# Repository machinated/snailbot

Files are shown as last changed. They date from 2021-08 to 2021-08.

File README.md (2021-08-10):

# snailbot
Arduino compatible robot platform

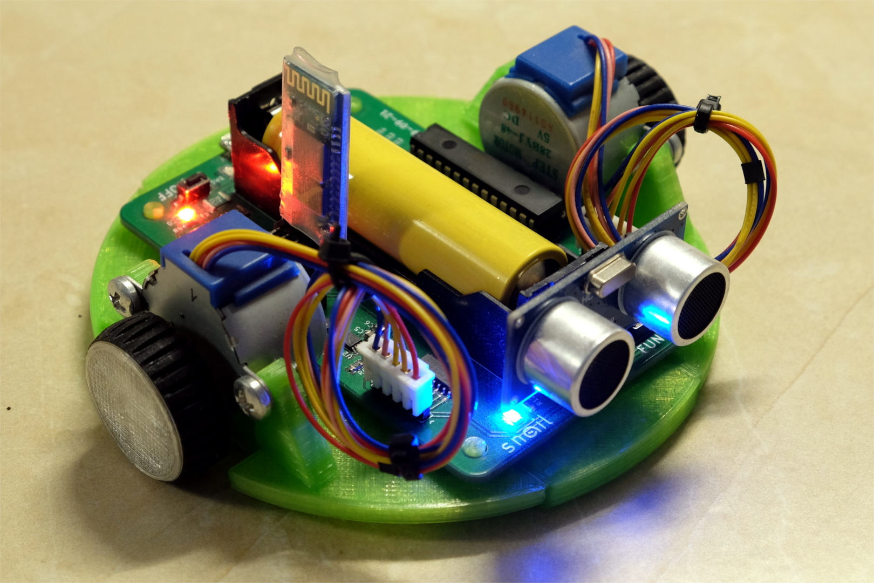
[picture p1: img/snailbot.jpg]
snailbot picture


## Hardware
List of parts:
 - electronic components listed in the [BOM file](pcb/BOM.csv)
 - HC-SR04 ultrasonic distance sensor
 - HC05 bluetooth adapter
 - 18650 lithium-ion battery
 - 2x 28BYJ-48 stepper motors

## Dependencies
- AccelStepper v.1.59

## Chassis
For better traction, use TPU for the tires.

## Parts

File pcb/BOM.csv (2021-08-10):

Item | Qty | Reference(s) | Value | Footprint
1 | 1 | BT1 | Battery_Cell | mc_mech:BatteryHolder_1x18650
2 | 1 | C1 | 4u7 | Capacitor_SMD:C_0805_2012Metric_Pad1.15x1.40mm_HandSolder
3 | 5 | C2, C4, C5, C6, C7 | 10u | Capacitor_SMD:C_0805_2012Metric_Pad1.15x1.40mm_HandSolder
4 | 4 | C8, C9, C10, C13 | 100n | Capacitor_SMD:C_0805_2012Metric_Pad1.15x1.40mm_HandSolder
5 | 2 | C11, C12 | 22p | Capacitor_SMD:C_0805_2012Metric_Pad1.15x1.40mm_HandSolder
6 | 1 | D1 | RED | LED_SMD:LED_1206_3216Metric_Pad1.42x1.75mm_HandSolder
7 | 1 | D2 | D_TVS | Diode_SMD:D_SMB_Handsoldering
8 | 1 | D3 | YELLOW | LED_SMD:LED_1206_3216Metric_Pad1.42x1.75mm_HandSolder
9 | 2 | D4, D5 | BLUE | LED_SMD:LED_1206_3216Metric_Pad1.42x1.75mm_HandSolder
10 | 1 | F1 | 750mA | Fuse:Fuse_1812_4532Metric_Pad1.30x3.40mm_HandSolder
11 | 1 | F2 | 1A | Fuse:Fuse_1812_4532Metric_Pad1.30x3.40mm_HandSolder
12 | 1 | J1 | USB_B_Micro | mc_mech:USB_Micro-B_MOLEX_105017-0001
13 | 1 | J2 | Conn_01x04_Female | Connector_PinHeader_2.54mm:PinHeader_1x04_P2.54mm_Vertical
14 | 2 | J3, J5 | Conn_01x05_Male | Connector_PinHeader_2.54mm:PinHeader_1x05_P2.54mm_Vertical
15 | 1 | J4 | Conn_01x06_Female | Connector_PinHeader_2.54mm:PinHeader_1x06_P2.54mm_Vertical
16 | 1 | L1 | 4u7 | Inductor_SMD:L_1210_3225Metric_Pad1.42x2.65mm_HandSolder
17 | 3 | R4, R9, R12 | 470 | Resistor_SMD:R_0805_2012Metric_Pad1.15x1.40mm_HandSolder
18 | 1 | R2 | 2k2 | Resistor_SMD:R_0805_2012Metric_Pad1.15x1.40mm_HandSolder
19 | 1 | R3 | 470k 1% | Resistor_SMD:R_0805_2012Metric_Pad1.15x1.40mm_HandSolder
20 | 1 | R5 | 1M | Resistor_SMD:R_0805_2012Metric_Pad1.15x1.40mm_HandSolder
21 | 1 | R6 | 150k 1% | Resistor_SMD:R_0805_2012Metric_Pad1.15x1.40mm_HandSolder
22 | 2 | R1, R7 | 1k | Resistor_SMD:R_0805_2012Metric_Pad1.15x1.40mm_HandSolder
23 | 1 | R8 | 100k | Resistor_SMD:R_0805_2012Metric_Pad1.15x1.40mm_HandSolder
24 | 3 | R10, R13, R15 | 10k | Resistor_SMD:R_0805_2012Metric_Pad1.15x1.40mm_HandSolder
25 | 1 | R11 | 15k | Resistor_SMD:R_0805_2012Metric_Pad1.15x1.40mm_HandSolder
26 | 2 | R14, R16 | 100 | Resistor_SMD:R_0805_2012Metric_Pad1.15x1.40mm_HandSolder
27 | 3 | SW1, SW2, SW3 | SW_Push | Button_Switch_SMD:SW_SPST_CK_RS282G05A3
28 | 1 | U1 | MCP73831-2-OT | Package_TO_SOT_SMD:SOT-23-5
29 | 1 | U2 | MCP1642B | Package_SO:MSOP-8-1EP_3x3mm_P0.65mm_EP2.54x2.8mm
30 | 2 | U3, U5 | ULN2003 | Package_SO:SOIC-16_3.9x9.9mm_P1.27mm
31 | 1 | U4 | ATmega328P-PU | Package_DIP:DIP-28_W7.62mm
32 | 1 | Y1 | 16MHz | Crystal:Crystal_HC49-U_Vertical

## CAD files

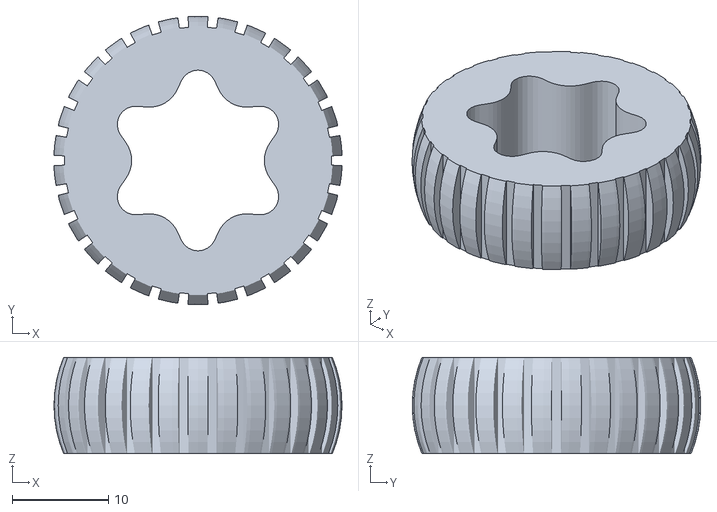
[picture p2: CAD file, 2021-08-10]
3d/stl/tire.stl
30.0 x 30.0 x 10.0

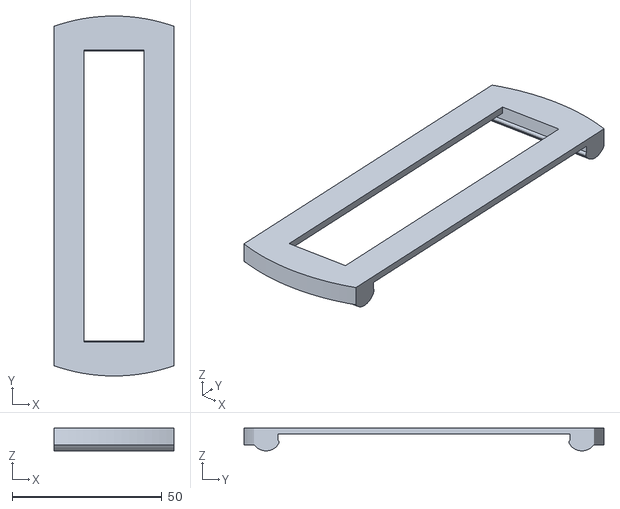
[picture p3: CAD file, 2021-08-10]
3d/stl/chassis_p2.stl
39.9 x 120.0 x 7.60

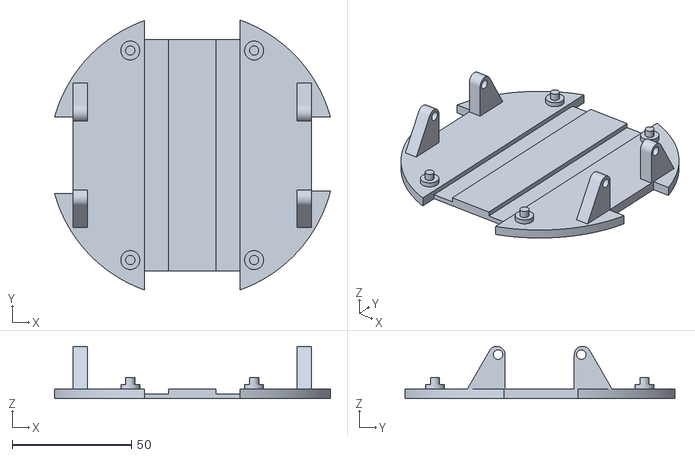
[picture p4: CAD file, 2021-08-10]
3d/stl/chassis_p1.stl
115.9 x 113.4 x 22.0

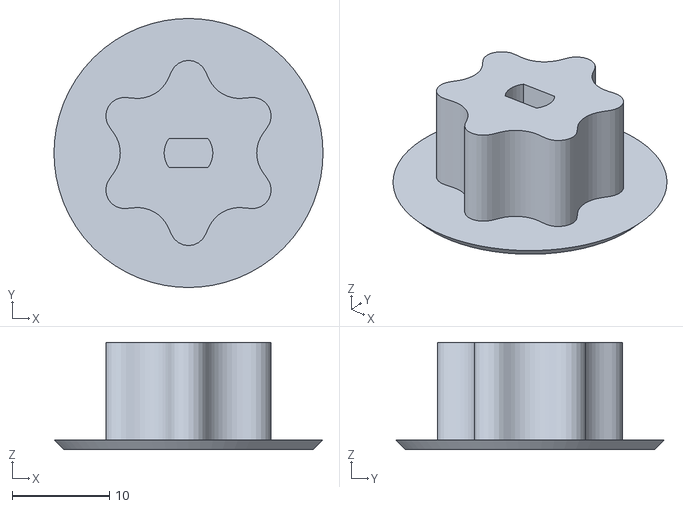
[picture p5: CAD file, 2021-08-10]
3d/stl/wheel.stl
27.6 x 27.6 x 11.0

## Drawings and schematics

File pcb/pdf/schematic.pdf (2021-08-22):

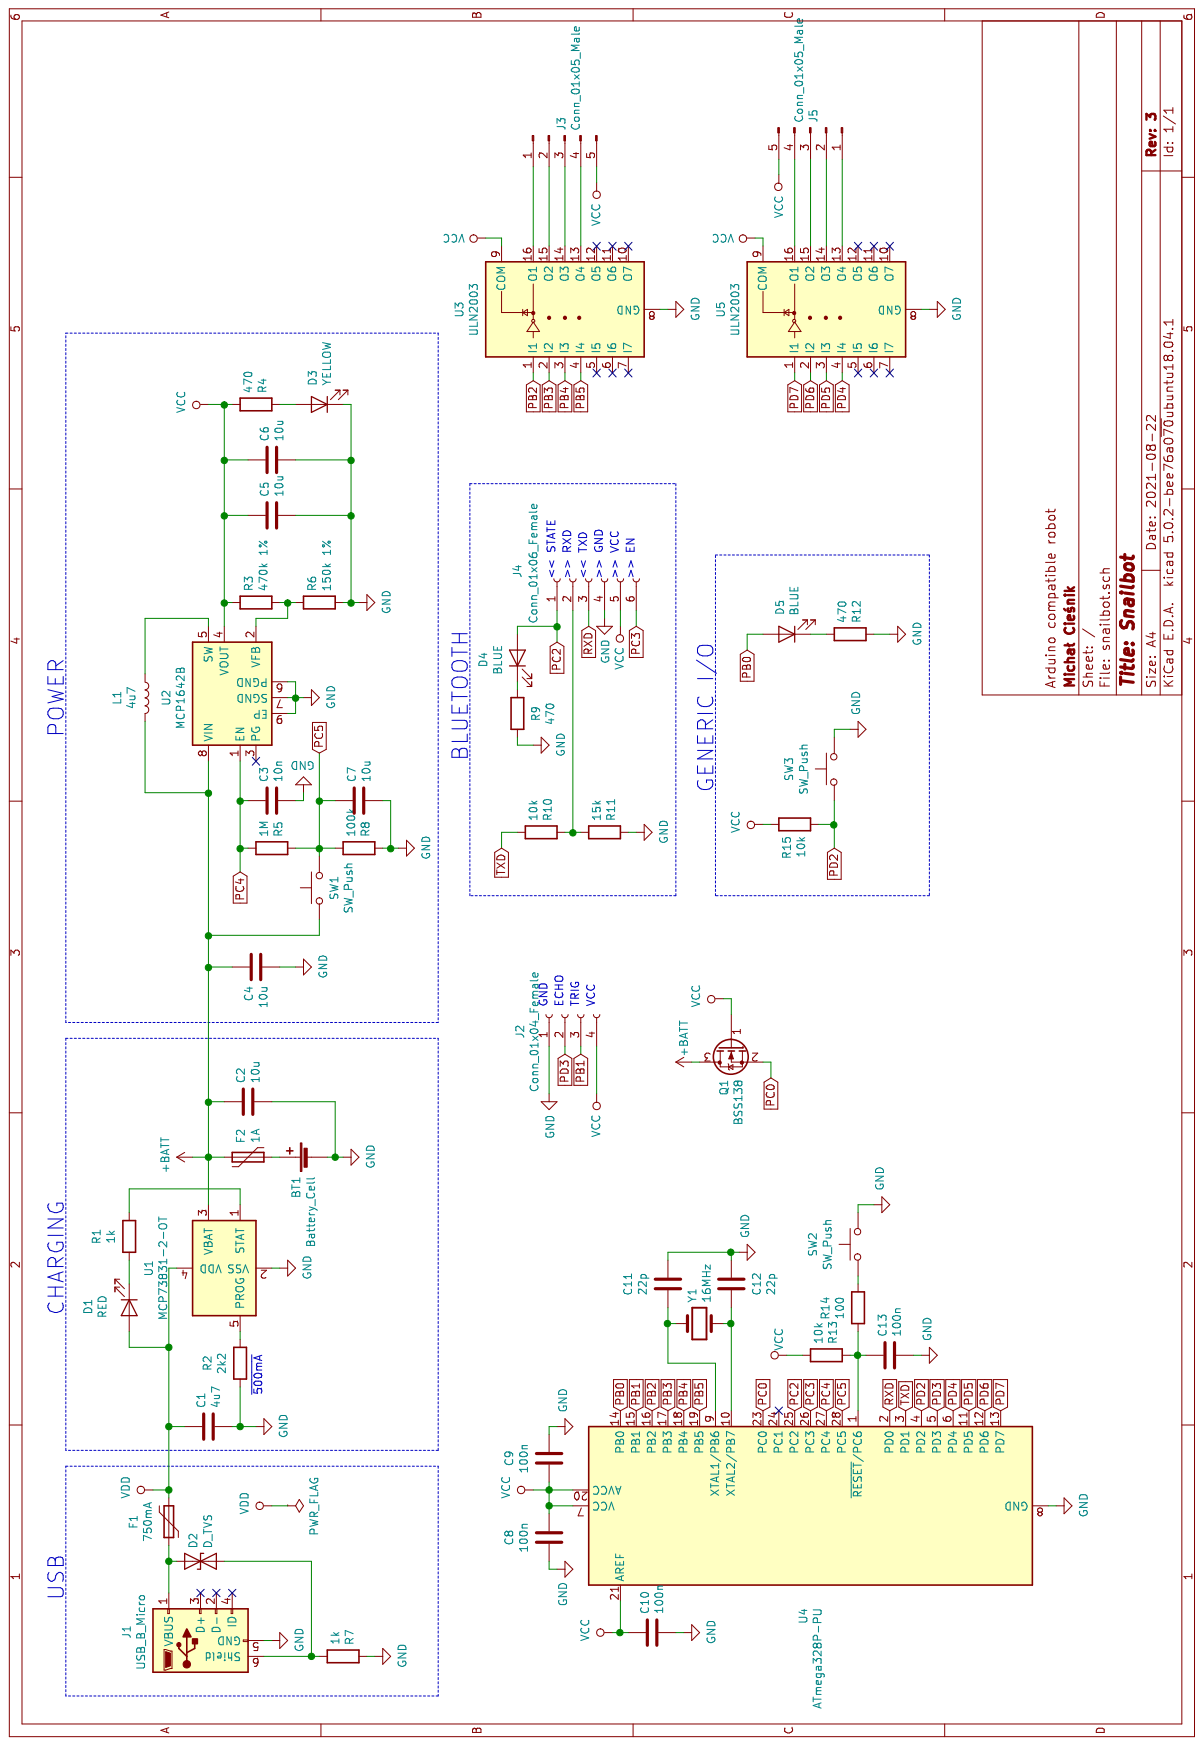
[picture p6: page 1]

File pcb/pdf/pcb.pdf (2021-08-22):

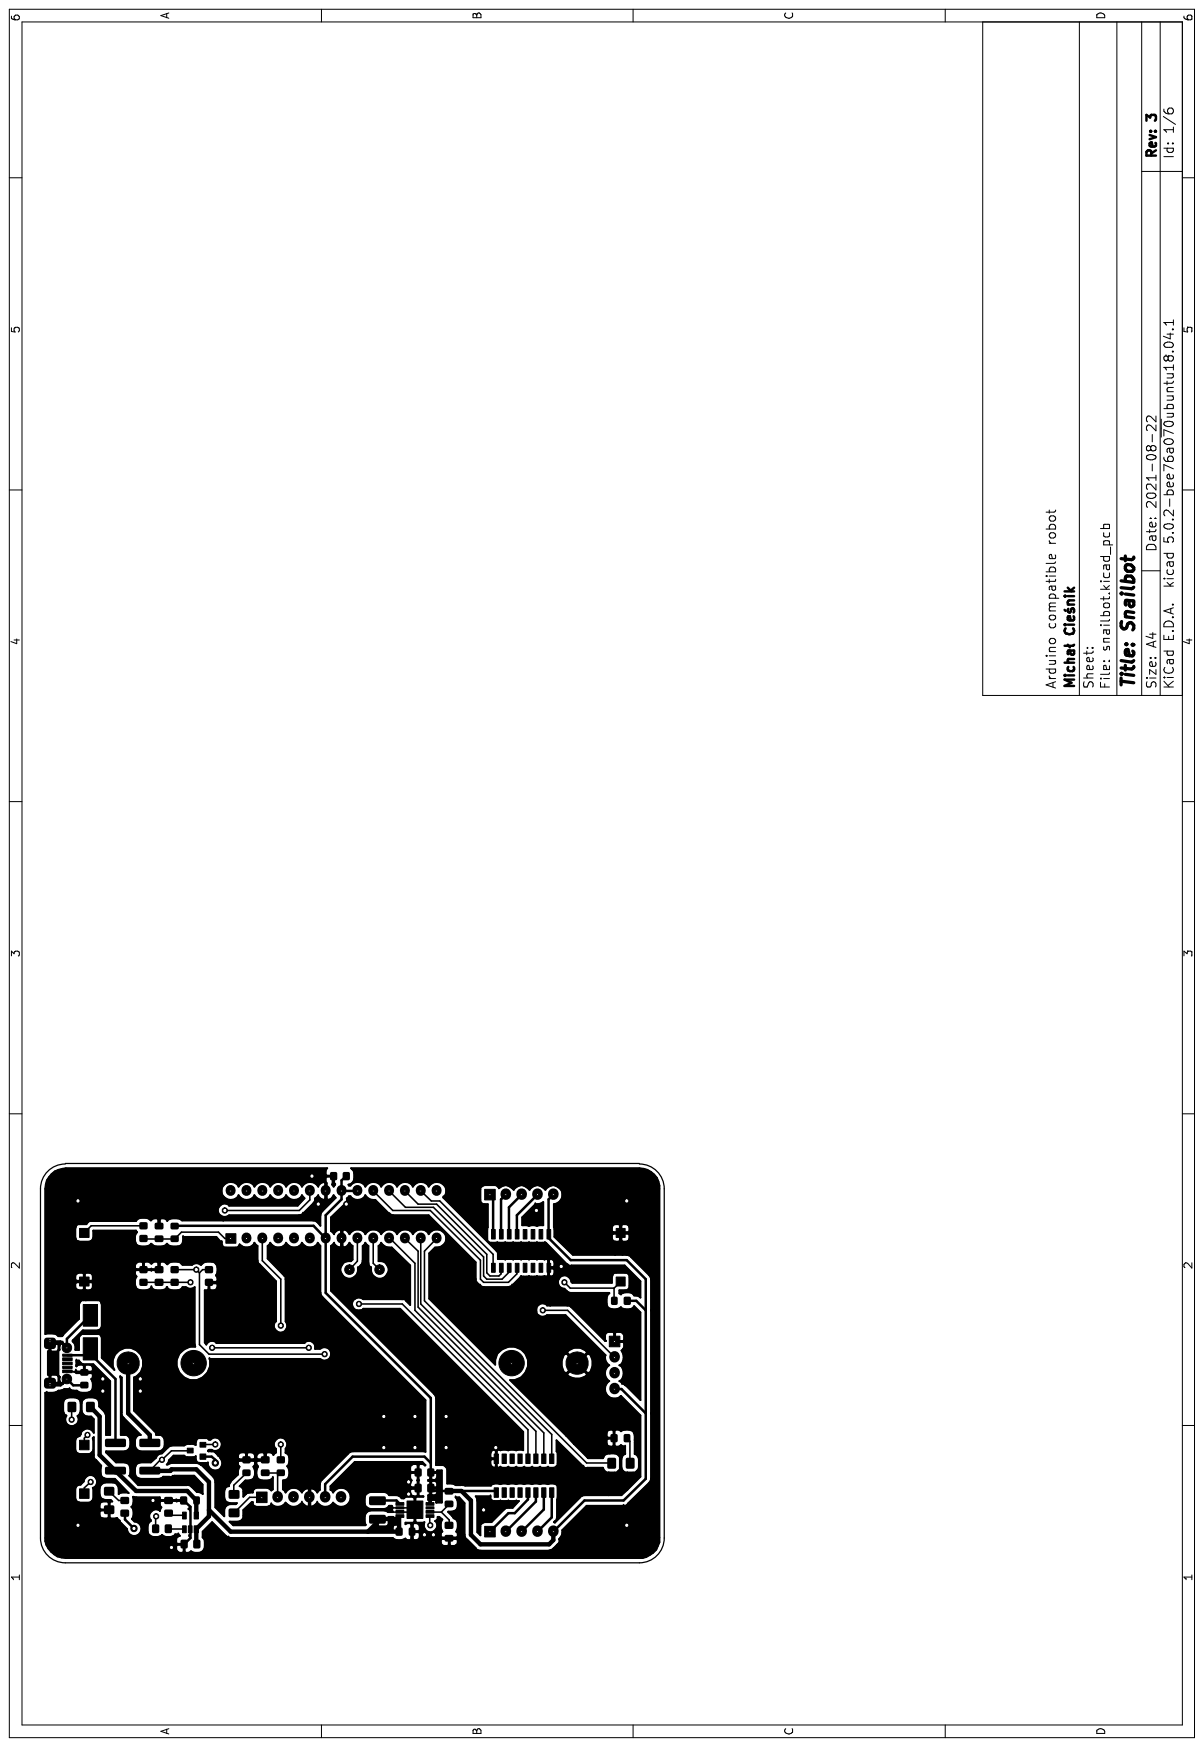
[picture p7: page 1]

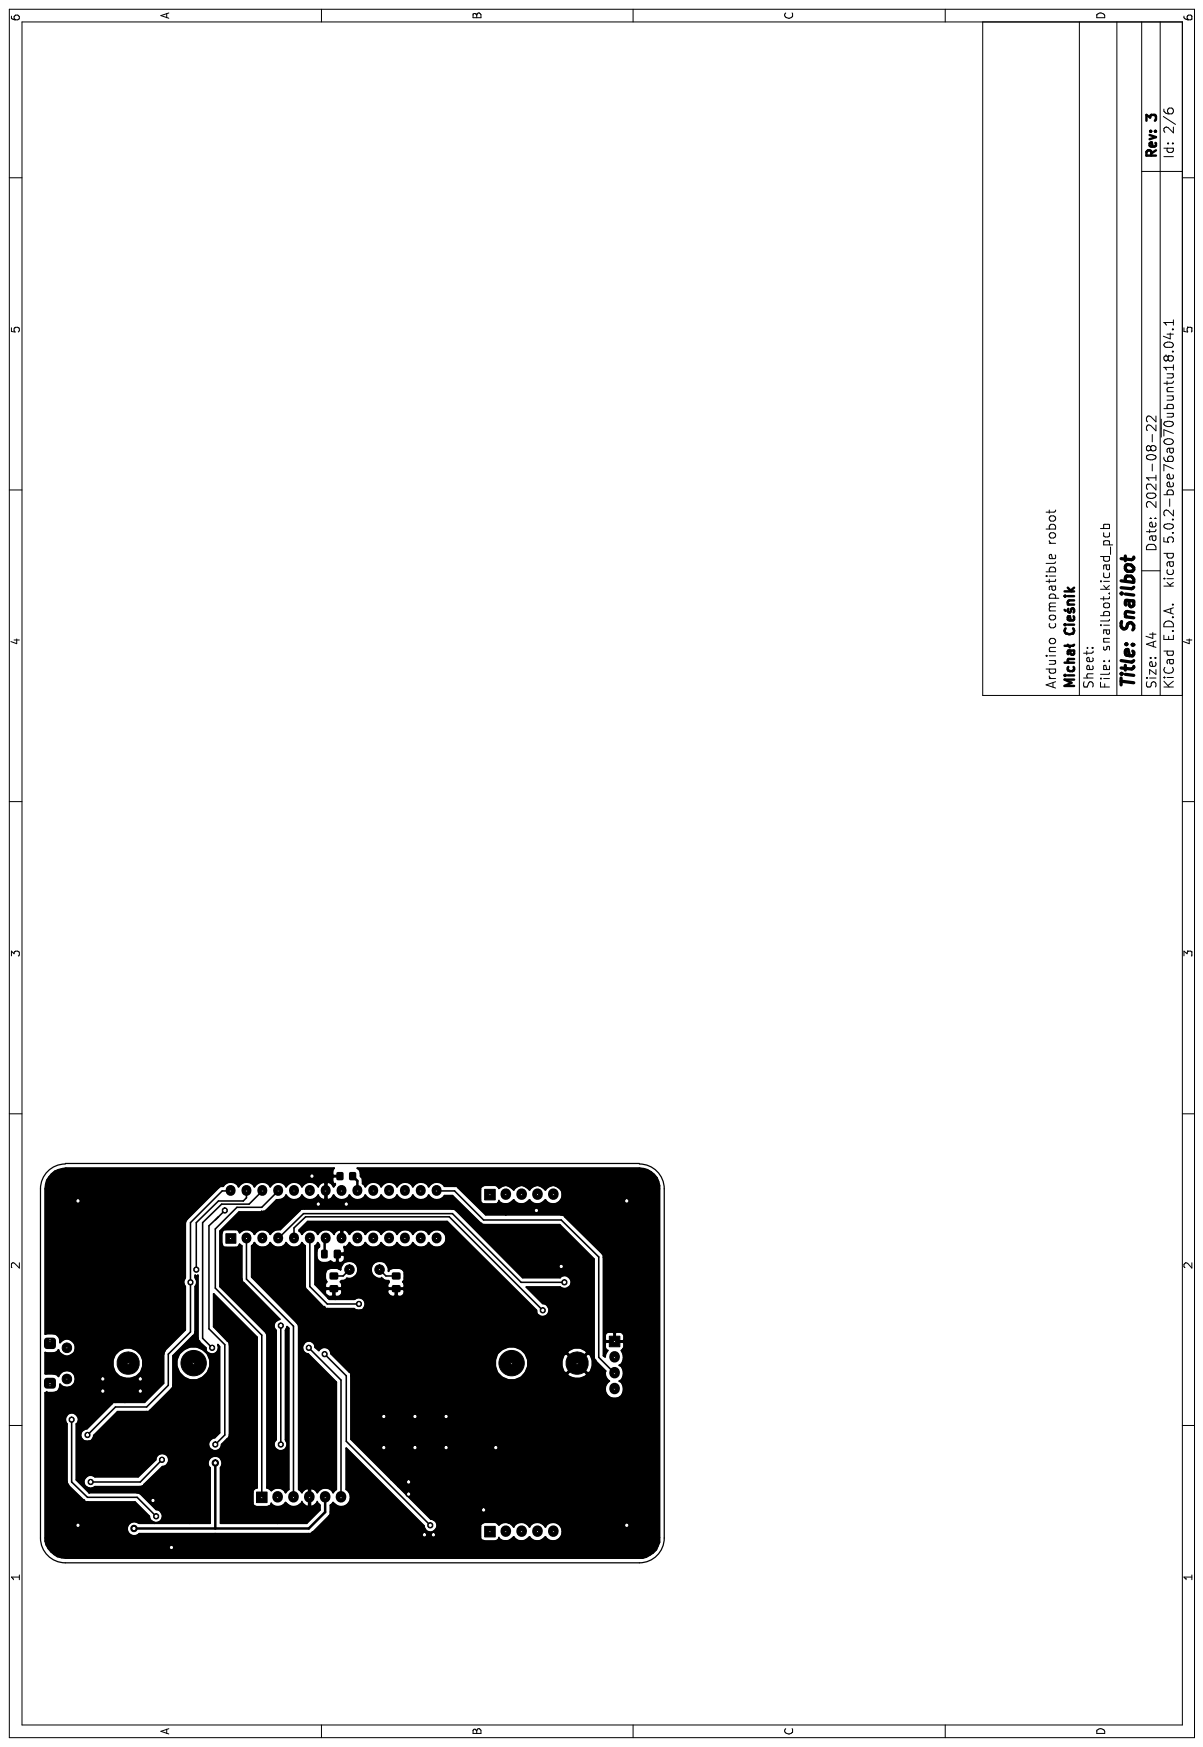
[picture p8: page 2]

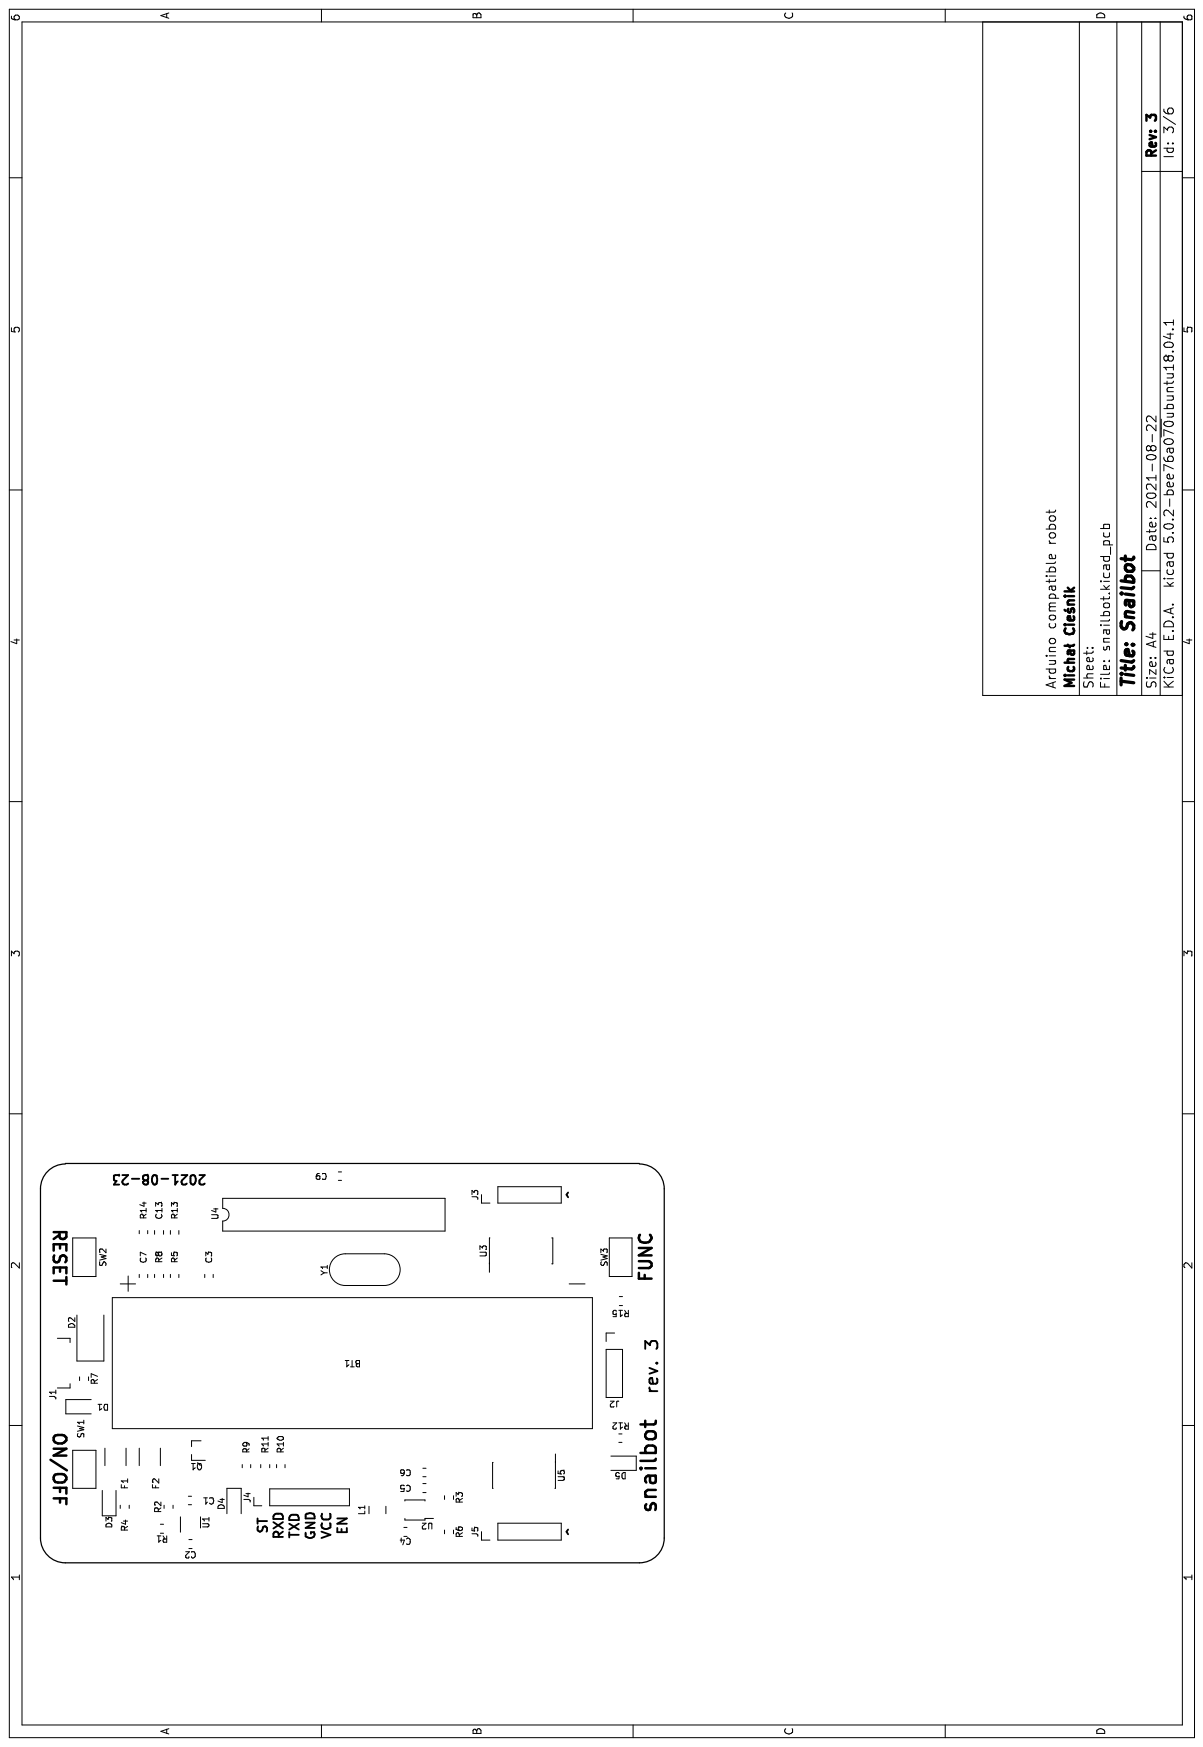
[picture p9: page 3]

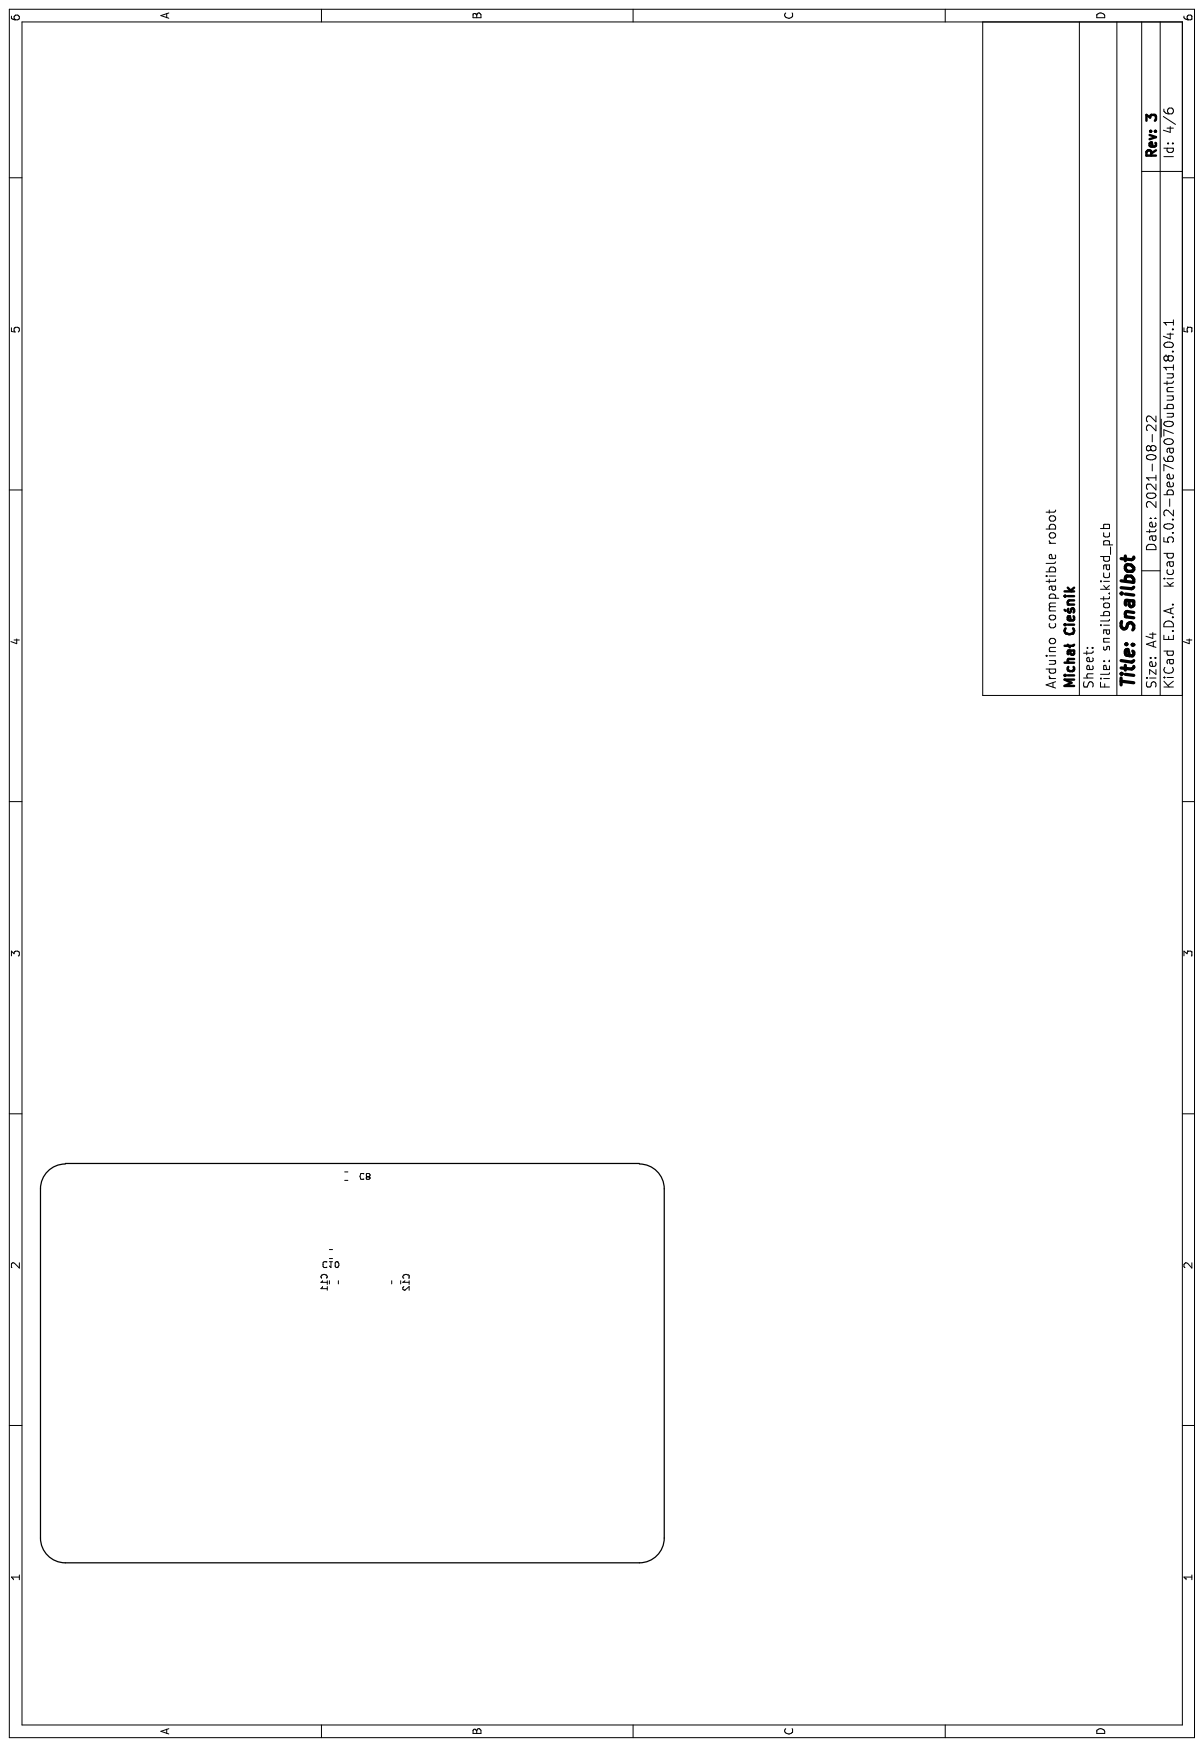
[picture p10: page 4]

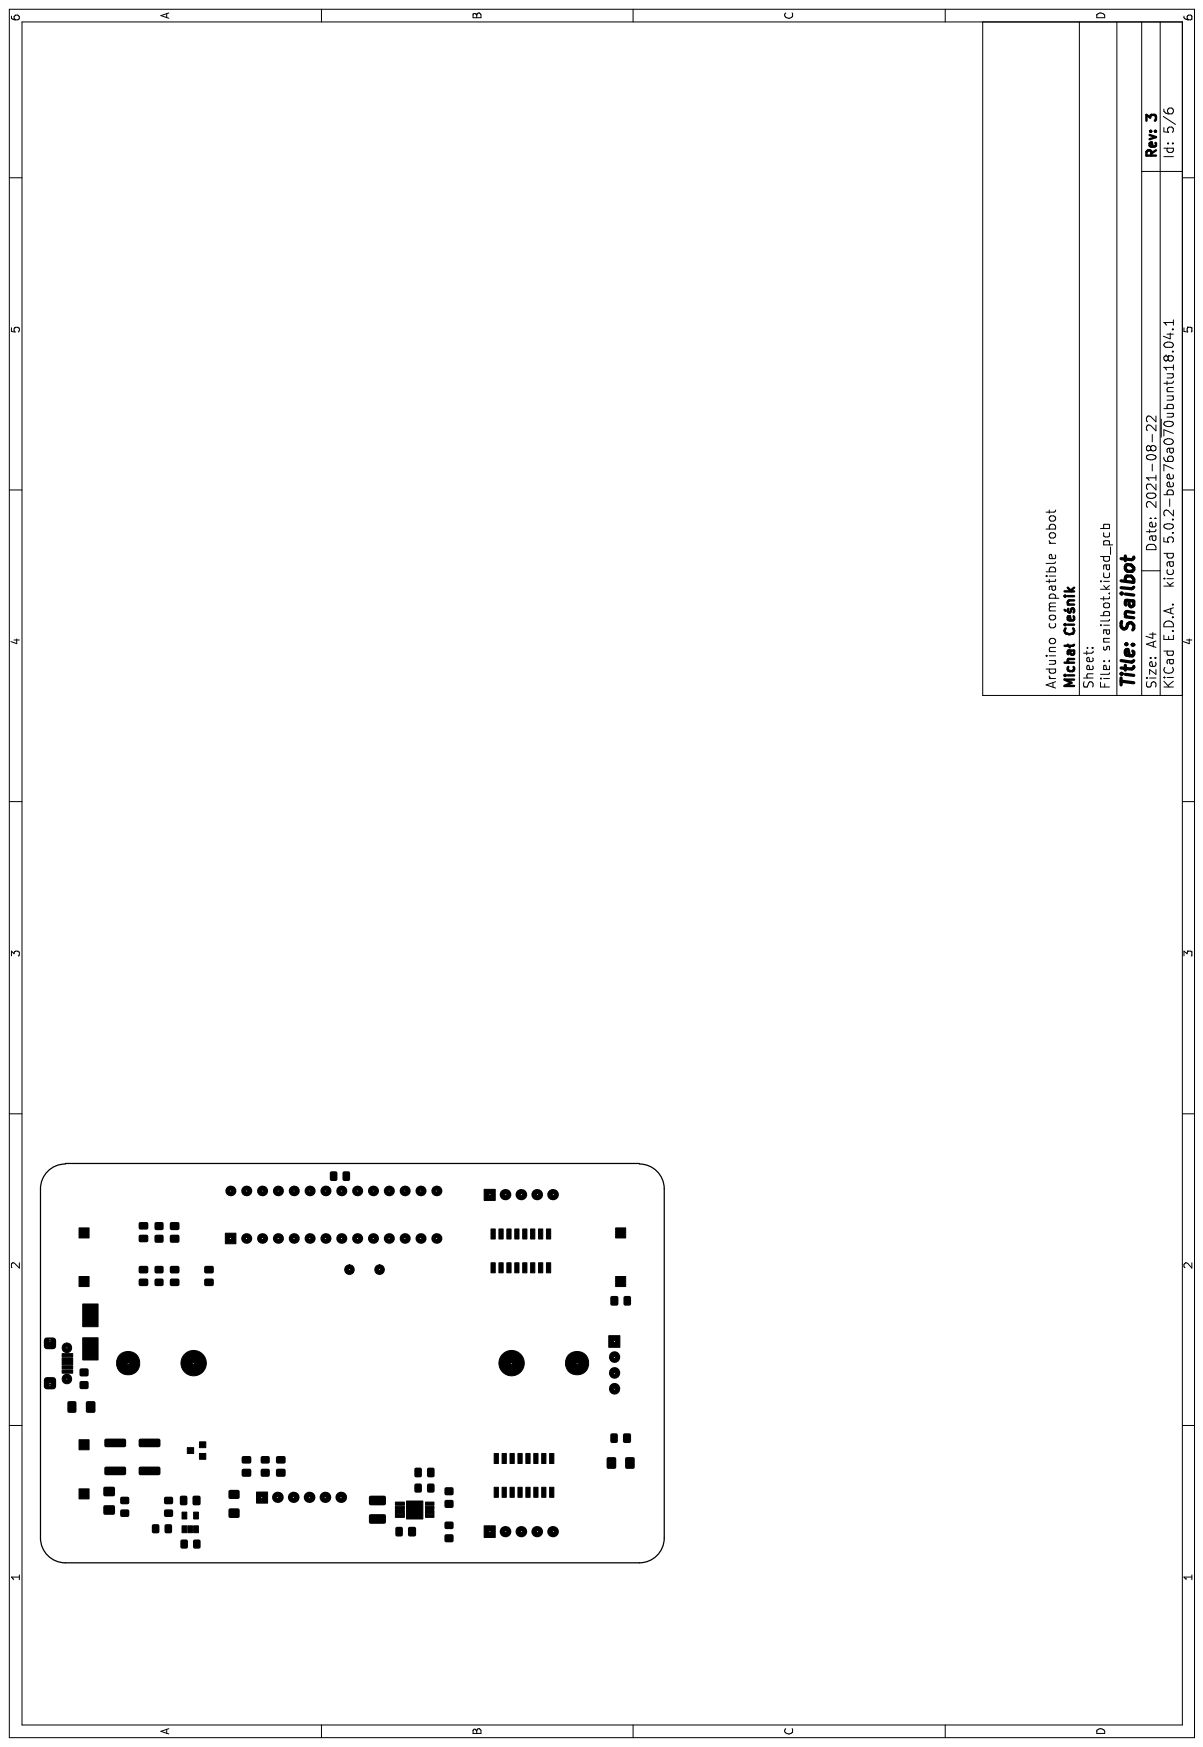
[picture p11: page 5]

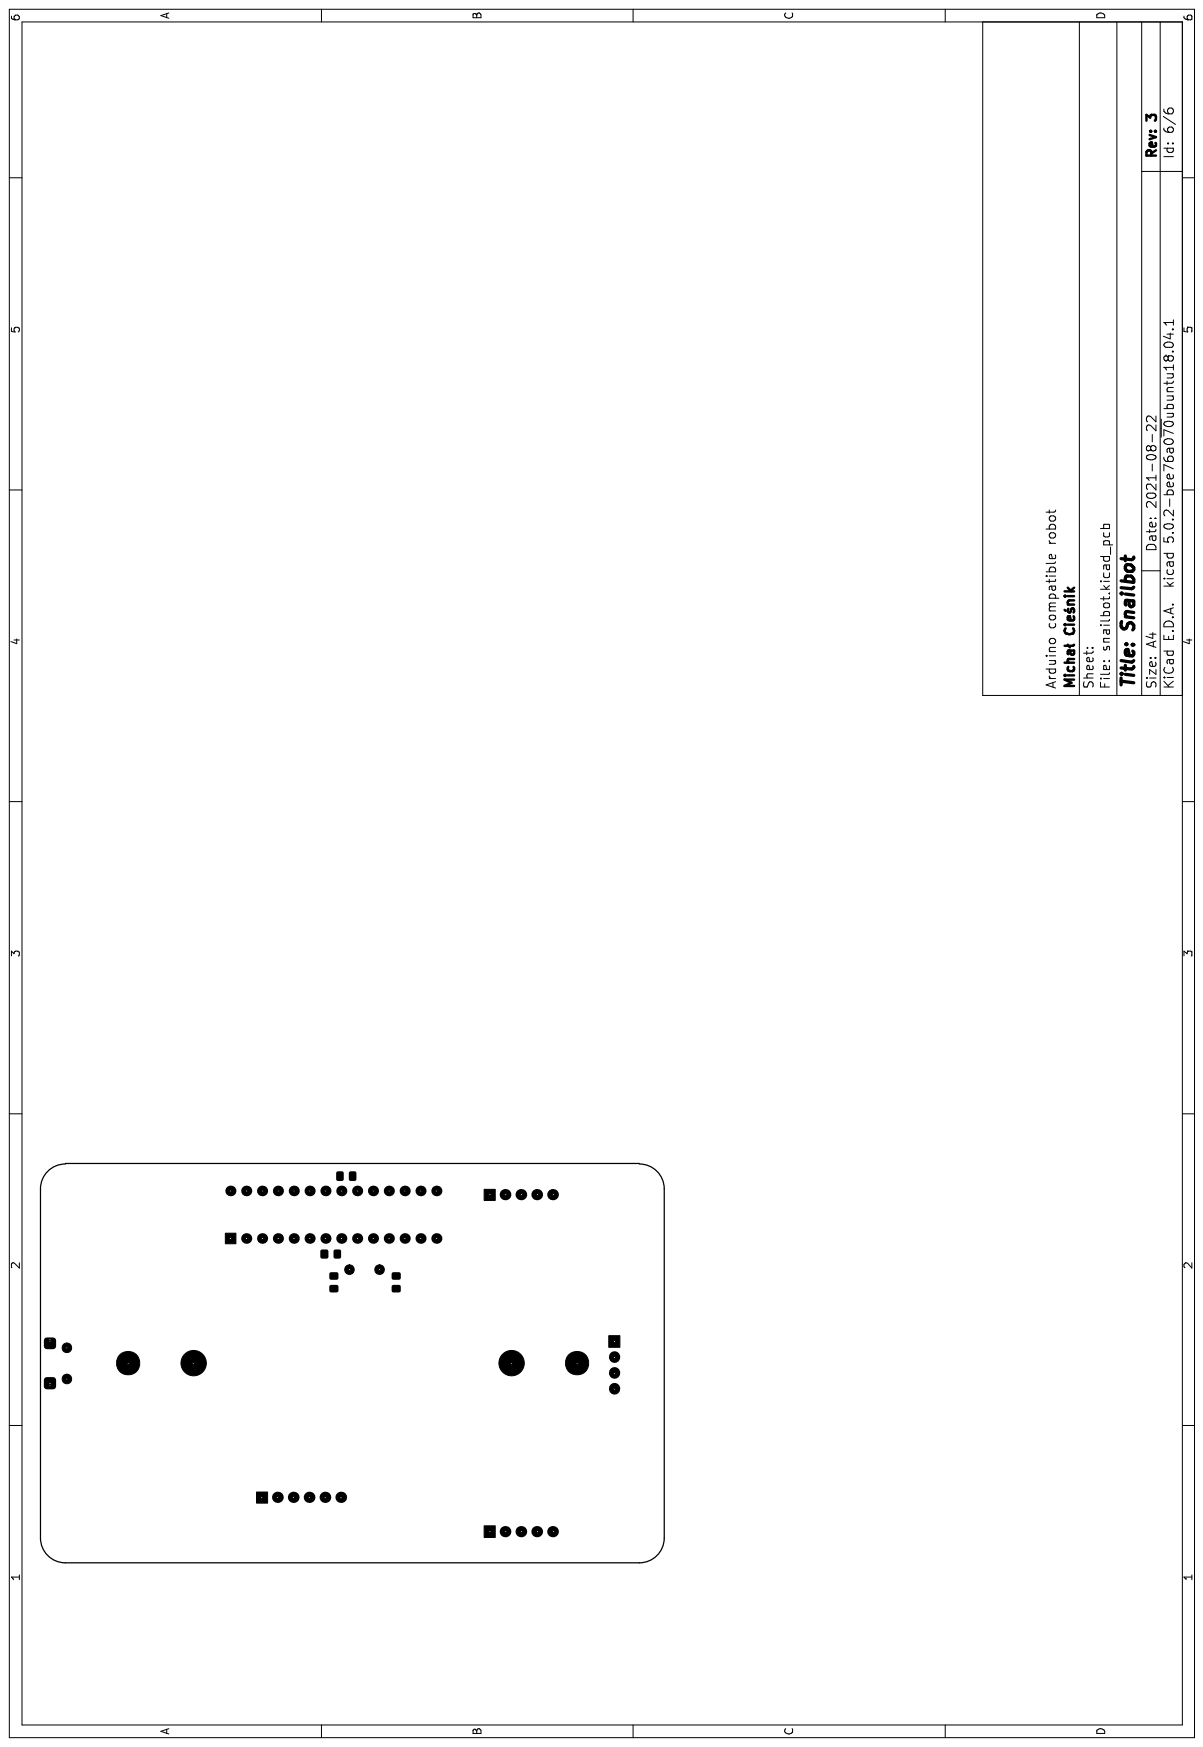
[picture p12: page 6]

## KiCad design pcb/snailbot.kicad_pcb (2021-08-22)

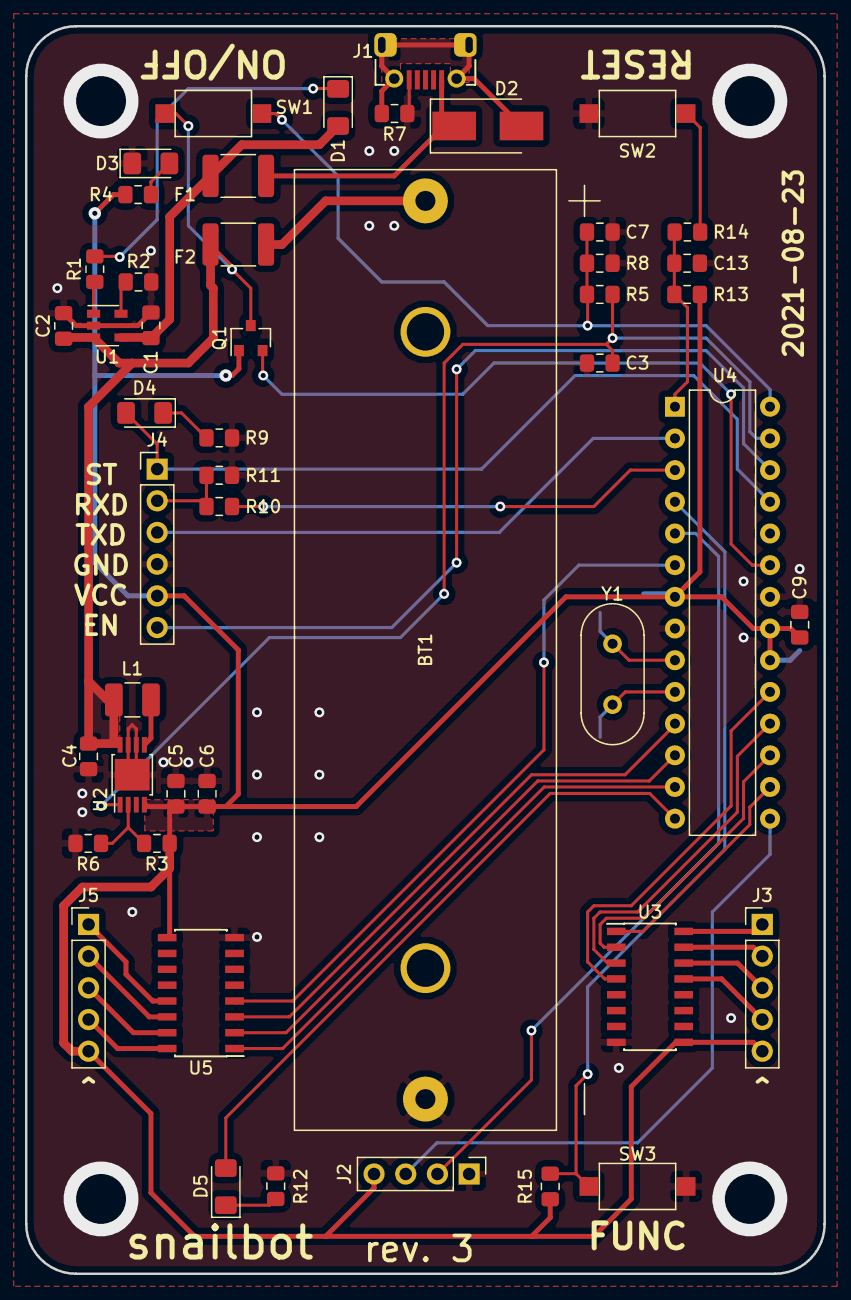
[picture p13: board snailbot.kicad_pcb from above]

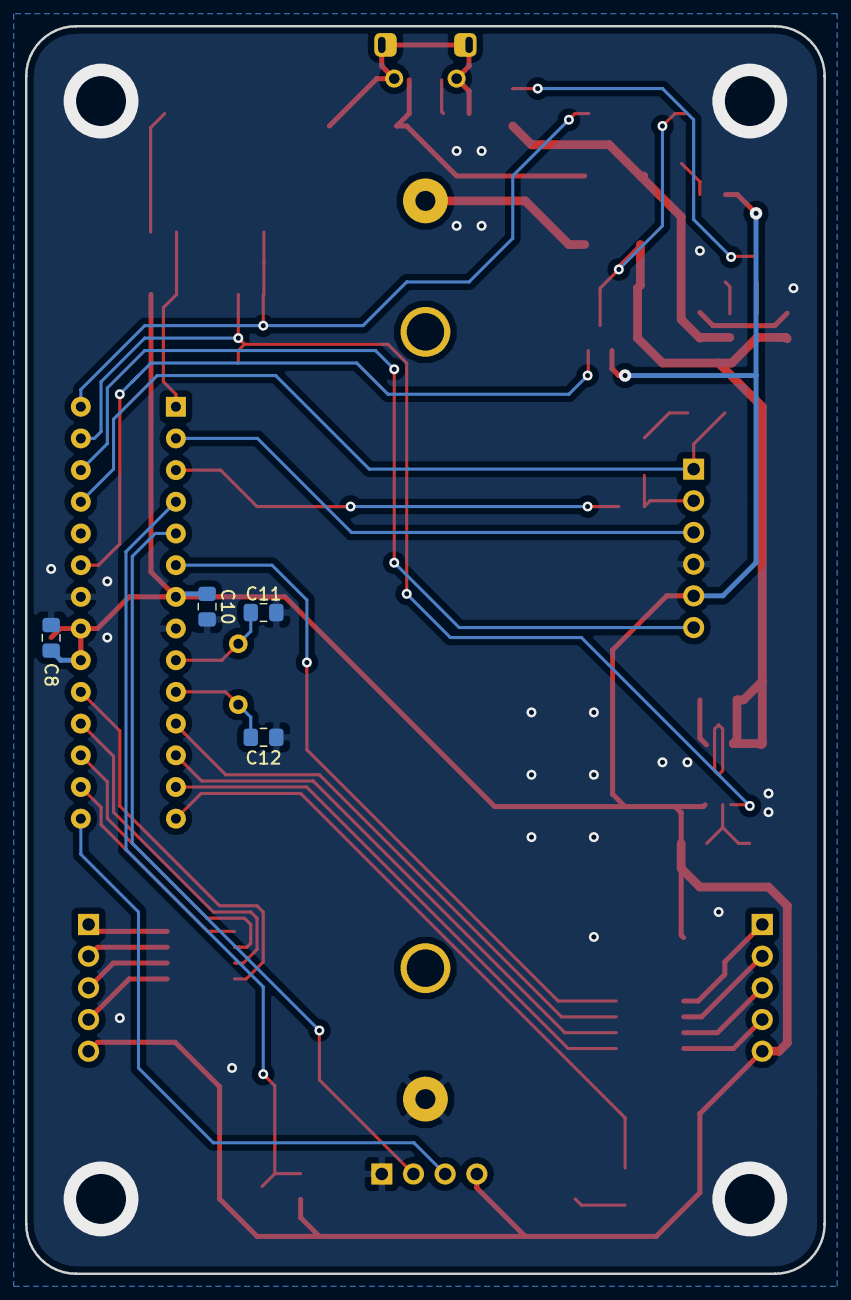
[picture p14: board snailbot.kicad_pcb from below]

Board: 2 copper layers, 64.0 x 100.0 mm, 52 parts (4 on the bottom side), 47 nets.

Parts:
BT1: Battery_Cell; BatteryHolder_1x18650
C1: 4u7; C_0805_2012Metric_Pad1.15x1.40mm_HandSolder
C2, C4, C5, C6, C7: 10u; C_0805_2012Metric_Pad1.15x1.40mm_HandSolder
C3: 10n; C_0805_2012Metric_Pad1.15x1.40mm_HandSolder
C8, C9, C10, C13: 100n; C_0805_2012Metric_Pad1.15x1.40mm_HandSolder
C11, C12: 22p; C_0805_2012Metric_Pad1.15x1.40mm_HandSolder
D1: RED; LED_1206_3216Metric_Pad1.42x1.75mm_HandSolder
D2: D_TVS; D_SMB_Handsoldering
D3: YELLOW; LED_1206_3216Metric_Pad1.42x1.75mm_HandSolder
D4, D5: BLUE; LED_1206_3216Metric_Pad1.42x1.75mm_HandSolder
F1: 750mA; Fuse_1812_4532Metric_Pad1.30x3.40mm_HandSolder
F2: 1A; Fuse_1812_4532Metric_Pad1.30x3.40mm_HandSolder
J1: USB_B_Micro; USB_Micro-B_MOLEX_105017-0001
J2: Conn_01x04_Female; PinHeader_1x04_P2.54mm_Vertical
J3, J5: Conn_01x05_Male; PinHeader_1x05_P2.54mm_Vertical
J4: Conn_01x06_Female; PinHeader_1x06_P2.54mm_Vertical
L1: 4u7; L_1210_3225Metric_Pad1.42x2.65mm_HandSolder
Q1: BSS138; SOT-23
R1, R7: 1k; R_0805_2012Metric_Pad1.15x1.40mm_HandSolder
R2: 2k2; R_0805_2012Metric_Pad1.15x1.40mm_HandSolder
R3: 470k 1%; R_0805_2012Metric_Pad1.15x1.40mm_HandSolder
R4, R9, R12: 470; R_0805_2012Metric_Pad1.15x1.40mm_HandSolder
R5: 1M; R_0805_2012Metric_Pad1.15x1.40mm_HandSolder
R6: 150k 1%; R_0805_2012Metric_Pad1.15x1.40mm_HandSolder
R8: 100k; R_0805_2012Metric_Pad1.15x1.40mm_HandSolder
R10, R13, R15: 10k; R_0805_2012Metric_Pad1.15x1.40mm_HandSolder
R11: 15k; R_0805_2012Metric_Pad1.15x1.40mm_HandSolder
R14: 100; R_0805_2012Metric_Pad1.15x1.40mm_HandSolder
SW1, SW2, SW3: SW_Push; SW_SPST_CK_RS282G05A3
U1: MCP73831-2-OT; SOT-23-5
U2: MCP1642B; MSOP-8-1EP_3x3mm_P0.65mm_EP2.54x2.8mm
U3, U5: ULN2003; SOIC-16_3.9x9.9mm_P1.27mm
U4: ATmega328P-PU; DIP-28_W7.62mm
Y1: 16MHz; Crystal_HC49-U_Vertical

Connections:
+BATT: C2.1, C4.1, F2.1, L1.2, Q1.3, SW1.1, U1.3, U2.8
GND: BT1.2, C1.2, C2.2, C3.1, C4.2, C5.2, C6.2, C7.2, C8.2, C9.1, C10.2, C11.1, C12.1, C13.2, D3.1, J1.5, J2.1, J4.4, R2.2, R6.2, R7.1, R8.1, R9.1, R11.1, R12.1, SW2.2, SW3.2, U1.2, U2.6, U2.7, U2.9, U3.8, U4.8, U4.22, U5.8
unnamed: BT1.1, F2.2
unnamed: C11.2, U4.9, Y1.1
unnamed: C12.2, U4.10, Y1.2
unnamed: C13.1, R13.1, R14.1, U4.1
unnamed: D1.1, R1.2
unnamed: D2.1, F1.2, J1.1
unnamed: D2.2, J1.6, R7.2
unnamed: D3.2, R4.1
unnamed: D4.1, R9.2
unnamed: D5.1, R12.2
unnamed: J3.1, U3.16
unnamed: J3.2, U3.15
unnamed: J3.3, U3.14
unnamed: J3.4, U3.13
unnamed: J4.2, R10.1, R11.2
unnamed: J5.1, U5.13
unnamed: J5.2, U5.14
unnamed: J5.3, U5.15
unnamed: J5.4, U5.16
unnamed: L1.1, U2.5
unnamed: R1.1, U1.1
unnamed: R2.1, U1.5
unnamed: R3.2, R6.1, U2.2
unnamed: R14.2, SW2.1
PB0: D5.2, U4.14
PB1: J2.3, U4.15
PB2: U3.1, U4.16
PB3: U3.2, U4.17
PB4: U3.3, U4.18
PB5: U3.4, U4.19
PC0: Q1.2, U4.23
PC2: D4.2, J4.1, U4.25
PC3: J4.6, U4.26
PC4: C3.2, R5.2, U2.1, U4.27
PC5: C7.1, R5.1, R8.2, SW1.2, U4.28
PD2: R15.1, SW3.1, U4.4
PD3: J2.2, U4.5
PD4: U4.6, U5.4
PD5: U4.11, U5.3
PD6: U4.12, U5.2
PD7: U4.13, U5.1
RXD: J4.3, U4.2
TXD: R10.2, U4.3
VCC: C5.1, C6.1, C8.1, C9.2, C10.1, J2.4, J3.5, J4.5, J5.5, Q1.1, R3.1, R4.2, R13.2, R15.2, U2.4, U3.9, U4.7, U4.20, U4.21, U5.9
VDD: C1.1, D1.2, F1.1, U1.4

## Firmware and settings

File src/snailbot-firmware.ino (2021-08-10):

/*******************************************************************************
*  Sn@il robot firmware
*
*  Copyright (C) 2021 Michał Cieśnik
*
*  Commands:
*     MOVE <DISTANCE>   -- Move the robot in a straigt line by the specified
*                          number of centimeters. Move forward if the argument
*                          is positive, backward if it is negative.
*
*     TURN <DEGREES>    -- Turn in place by the specified angle given in degrees.
*                          Turn left if the argument is positive, right if it
*                          is negative.
*
*     GOTO <DISTANCE>   -- Move forward or backward to reach the specified distance
*                          in centimiters from the nearest object in front.
*
*     LEFT <STEPS>      -- Move only the left motor by the given number of steps.
*
*     RIGHT <STEPS>     -- Move only the right motor by the given number of steps.
*
*     STOP              -- Abort the current movement command.
*
*     SPEED <STEPS/S>   -- Set the maximum speed of the motors.
                           The default is 1000 steps per second or 2.3 cm/s.
*
*     ACCEL <STEPS/^2>  -- Set the acceleration of the motors.
*                          The default is 2000 steps per second^2.
*
*     BATT              -- Print the measuered battery voltage.
*
*     DIST              -- Measure the disctance to the nearest object in front
*                          using the ultrasonic sensor and print the result.
*
*     OFF               -- Power off.
*/

#include <string.h>
#include <stdlib.h>

#include <AccelStepper.h>

#define POWER_ENABLE_PIN 18
#define POWER_BUTTON_PIN 19

#define TRIG_PIN 9
#define ECHO_PIN 3         /* can be attached to INT1, currently isn't */

#define BATTERY_PIN A0

#define LED_PIN 8
#define BUTTON_PIN 2

#define STEPS_PER_CM 439.41
#define STEPS_PER_DEGREE 45.98

#define MIN_BATTERY_VOLTAGE 461     /* 2.95V */

#define GOTO_UPDATE_INTERVAL 2000
#define DEFAULT_SPEED 1000
#define DEFAULT_ACCELERATION 2000

#define MOTOR_LEFT 0
#define MOTOR_RIGHT 1

typedef enum Command {
   COMMAND_NONE,
   COMMAND_MOVE,
   COMMAND_TURN,
   COMMAND_GOTO,
   COMMAND_STOP,
   COMMAND_LEFT,
   COMMAND_RIGHT,
   COMMAND_OFF
} Command;

Command currentCommand = COMMAND_NONE;

AccelStepper motorLeft(AccelStepper::HALF4WIRE, 10, 12, 13, 11);
AccelStepper motorRight(AccelStepper::HALF4WIRE, 7, 5, 4, 6);

char command[5];
char argument[5];
bool isArg;
byte inputLen;

/* Called on incoming serial data */
void serialEvent()
{
   while(Serial.available())
   {
      char inChar = (char)Serial.read();
      if (inChar == '\n')
      {
         if (isArg)
         {
            argument[inputLen] = '\0';
         }
         else
         {
            command[inputLen] = '\0';
         }
         isArg = false;
         inputLen = 0;
         parseInput();
      }
      else if (inChar == ' ' && !isArg)
      {
         command[inputLen] = '\0';
         isArg = true;
         inputLen = 0;
      }
      else if (inputLen < 5)
      {
         if (isArg)
         {
            argument[inputLen] = inChar;
         }
         else
         {
            command[inputLen] = inChar;
         }
         inputLen++;
      }
   }
}

void parseInput()
{
   long parsedArg = strtol(argument, NULL, 10);

   if (strncmp(command, "STOP", 5) == 0)
   {
      currentCommand = COMMAND_STOP;
      cmdStop();
   }
   /* Commands other than STOP cannot interrupt current command */
   else if (currentCommand != COMMAND_NONE) {
      Serial.println("Still executing previous command");
   }
   else if (strncmp(command, "LEFT", 5) == 0)
   {
      currentCommand = COMMAND_LEFT;
      cmdRunMotor(MOTOR_LEFT, parsedArg);
   }
   else if (strncmp(command, "RIGHT", 5) == 0)
   {
      currentCommand = COMMAND_RIGHT;
      cmdRunMotor(MOTOR_RIGHT, parsedArg);
   }
   else if (strncmp(command, "SPEED", 5) == 0)
   {
      cmdSetSpeed(parsedArg);
   }
   else if (strncmp(command, "ACCEL", 5) == 0)
   {
      cmdSetAcceleration(parsedArg);
   }
   else if (strncmp(command, "MOVE", 5) == 0)
   {
      currentCommand = COMMAND_MOVE;
      cmdMove(parsedArg);
   }
   else if (strncmp(command, "TURN", 5) == 0)
   {
      currentCommand = COMMAND_TURN;
      cmdTurn(parsedArg);
   }
   else if (strncmp(command, "GOTO", 5) == 0)
   {
      currentCommand = COMMAND_GOTO;
      cmdGoto(parsedArg);
   }
   else if (strncmp(command, "DIST", 5) == 0)
   {
      cmdDistance();
   }
   else if (strncmp(command, "BATT", 5) == 0)
   {
      cmdBatt();
   }
   else if (strncmp(command, "OFF", 5) == 0)
   {
      currentCommand = COMMAND_OFF;
      cmdPowerOff();
   }
   else
   {
      Serial.print("Unknown command: ");
      Serial.println(command);
   }
}

void cmdRunMotor(byte motor, long steps)
{
   if (motor == MOTOR_LEFT)
   {
      Serial.print("Advancing left motor by ");
      Serial.print(steps);
      Serial.println(" steps");
      motorLeft.move(steps);
   }
   else if (motor == MOTOR_RIGHT)
   {
      Serial.print("Advancing right motor by ");
      Serial.print(steps);
      Serial.println(" steps");
      motorRight.move(steps);
   }
   else
   {
      return;
   }
}

void cmdMove(int distance)
{
   long steps = (long) distance * STEPS_PER_CM;
   Serial.print("Moving by ");
   Serial.print(distance);
   Serial.println(" cm");
   motorLeft.move(steps);
   motorRight.move(steps);
}

void cmdStop()
{
   if (currentCommand == COMMAND_NONE)
   {
      Serial.println("Already stopped");
      return;
   }
   Serial.println("Stopping");
   motorLeft.stop();
   motorRight.stop();
}

long gotoLastUpdate;
int gotoTarget;

void cmdGoto(int targetDistance)
{
   Serial.print("Moving to distance ");
   Serial.print(targetDistance);
   Serial.println(" cm");
   gotoTarget = targetDistance;
   gotoUpdate();
}

void gotoUpdate()
{
   int moveBy = measureDistance() - gotoTarget;
   long steps = (long) moveBy * STEPS_PER_CM;
   motorLeft.move(steps);
   motorRight.move(steps);
}

void cmdTurn(int degrees)
{
   long steps = (long) degrees * STEPS_PER_DEGREE;
   Serial.print("Turning by ");
   Serial.print(degrees);
   Serial.println(" degrees.");
   motorLeft.move(-steps);
   motorRight.move(steps);
}

void cmdSetSpeed(float speed)
{
   Serial.print("Speed set to ");
   Serial.println(speed);
   motorLeft.setMaxSpeed(speed);
   motorRight.setMaxSpeed(speed);
}

void cmdSetAcceleration(float acceleration)
{
   Serial.print("Acceleration set to ");
   Serial.println(acceleration);
   motorLeft.setAcceleration(acceleration);
   motorRight.setAcceleration(acceleration);
}

void cmdDistance()
{
   Serial.print("Distance: ");
   Serial.print(measureDistance());
   Serial.println(" cm");
}

void cmdBatt()
{
   int reading = analogRead(BATTERY_PIN);
   float voltage = (reading * 5.0) / 1024 + 0.7;
   Serial.print("Battery voltage: ");
   Serial.print(voltage, 2);
   Serial.println("V");
}

void cmdPowerOff()
{
   Serial.println("Powering off now. Bye bye...");
   powerOff();
}

int measureDistance()
{
   digitalWrite(TRIG_PIN, LOW);
   delayMicroseconds(5);
   digitalWrite(TRIG_PIN, HIGH);
   delayMicroseconds(10);
   digitalWrite(TRIG_PIN, LOW);
   long duration = pulseIn(ECHO_PIN, HIGH);
   return (int) duration / 58.2;
}

void powerOff()
{
   for(int i=0; i<4 || digitalRead(POWER_BUTTON_PIN); i++)
   {
      /* flash LED */
      digitalWrite(LED_PIN, LOW);
      delay(125);
      digitalWrite(LED_PIN, HIGH);
      delay(125);
   }
   digitalWrite(LED_PIN, LOW);
   delay(500);
   digitalWrite(POWER_ENABLE_PIN, LOW);
   pinMode(POWER_ENABLE_PIN, INPUT);
   while(true)
   {
      ;           /* wait for regulator shutdown */
   }
}

long lastBlink = 0;
bool ledOn = false;
byte cycle = 0;

/* Arduino library will execute function named 'setup' once at the start */
void setup()
{
   pinMode(POWER_ENABLE_PIN, OUTPUT);
   pinMode(TRIG_PIN, OUTPUT);
   pinMode(LED_PIN, OUTPUT);

   /* keep power regulator on after power button is released */
   digitalWrite(POWER_ENABLE_PIN, HIGH);
   digitalWrite(LED_PIN, HIGH);

   if (!digitalRead(POWER_BUTTON_PIN))
   {
      powerOff();
   }

   while(digitalRead(POWER_BUTTON_PIN))  /* wait for power button release */
   {
      delay(1);
   }
   digitalWrite(LED_PIN, LOW);

   motorLeft.setMaxSpeed(DEFAULT_SPEED);
   motorRight.setMaxSpeed(DEFAULT_SPEED);
   motorLeft.setAcceleration(DEFAULT_ACCELERATION);
   motorRight.setAcceleration(DEFAULT_ACCELERATION);

   Serial.begin(9600);
   /* ignore the starting "ATAT" sent by bluetooth adapter */
   Serial.readBytes((char*) NULL, 10);
   Serial.println("Sn@il firmware version 0.4.0");
   Serial.println("Accepting commands.");

   lastBlink = millis();
}

/* Arduion library will execute this function continuously after setup() returns */
void loop()
{
   /* check battery voltage once every 256 loops */
   if (cycle++ == 0 && analogRead(BATTERY_PIN) < MIN_BATTERY_VOLTAGE)
   {
      Serial.println("Battery critical. Powering off.");
      powerOff();
   }
   if (digitalRead(POWER_BUTTON_PIN))
   {
      Serial.println("Manual power off.");
      powerOff();
   }
   /* blink the status LED every 1s */
   if (millis() - lastBlink >= 1000)
   {
      lastBlink = millis();
      ledOn = !ledOn;
      digitalWrite(LED_PIN, ledOn);
   }
   if (currentCommand == COMMAND_GOTO)
   {
      if (abs(motorLeft.currentPosition() - gotoLastUpdate) >= GOTO_UPDATE_INTERVAL)
      {
         gotoLastUpdate = motorLeft.currentPosition();
         gotoUpdate();
      }
   }
   if (currentCommand != COMMAND_NONE && !motorLeft.isRunning() && !motorRight.isRunning())
   {
      currentCommand = COMMAND_NONE;
      Serial.println("Done");
      motorLeft.disableOutputs();
      motorRight.disableOutputs();
   }
   motorLeft.run();
   motorRight.run();
}

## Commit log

2021-08-10 Initial sources and designs
    [BOM.csv, chassis_p1.stl, chassis_p2.stl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]
2021-08-22 Fixed issues found in prototype
    [snailbot.kicad_pcb, snailbot.sch]
2021-08-22 Updated schematics and production files
    [snailbot-B.Cu.gbl, snailbot-B.Mask.gbs, snailbot-B.SilkS.gbo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]
